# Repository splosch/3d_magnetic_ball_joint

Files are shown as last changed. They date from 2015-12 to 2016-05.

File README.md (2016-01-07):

# 3d_magnetic_ball_joint
Low-friction magnetic ball joints for delta 3d printer based on standard components

## information on the parts / examples
The assebled / example screens are indicate a scheme but might not contain the most recent part updates.
The 123DX and STL files reflect the latest updates.

## Design B: conic magnet with epoxy coating
Chromeball sliding directly on a epoxyd cylindric magnet with a conical hole where the ball snapps in

* Pro:
  * cheap standard components
  * ball is hold tight and is keept centered
  * N42 magnets provide enough stength to keep up with high printing speeds / accelerations
  * screw to maintain magnet holder pockets are reachable through magnet hole
* Contra:
  * potential wear from opertion on the epoxy coating
    * it's conical, not spherical so friction is not distributed equally
    * silikon lubrication or PTFE (Teflon) spray-paint-coating on top of the epoxy could help
  * in current design the magnet is press-fit in the pocket
    * A) tighten the screw leaves tiny traces from inserting/extrating screwdriver

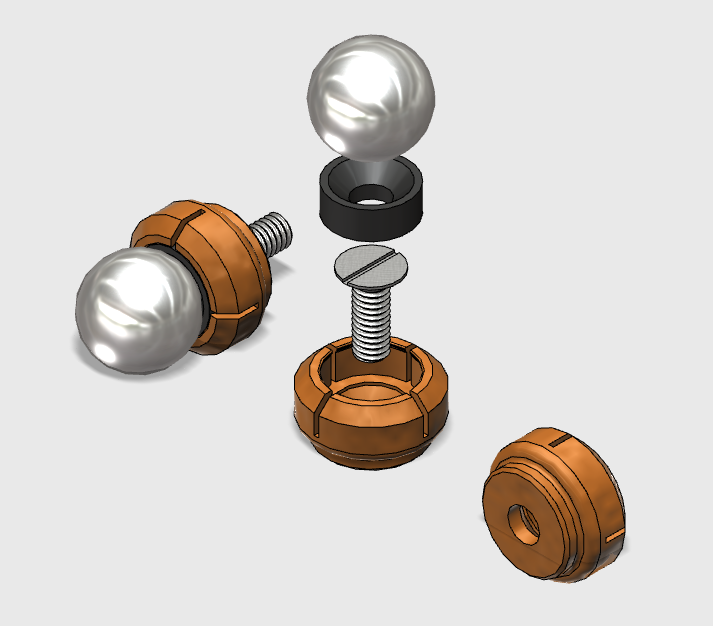
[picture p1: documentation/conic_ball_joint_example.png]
B) conic ball joint example


### Example: end effector
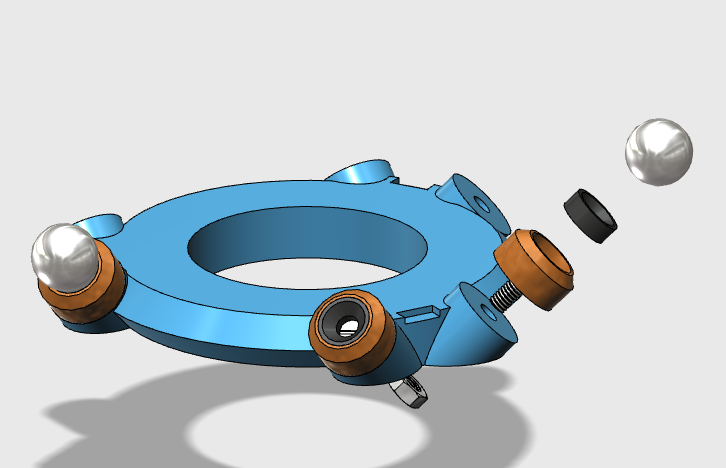
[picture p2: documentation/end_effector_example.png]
end effector example image


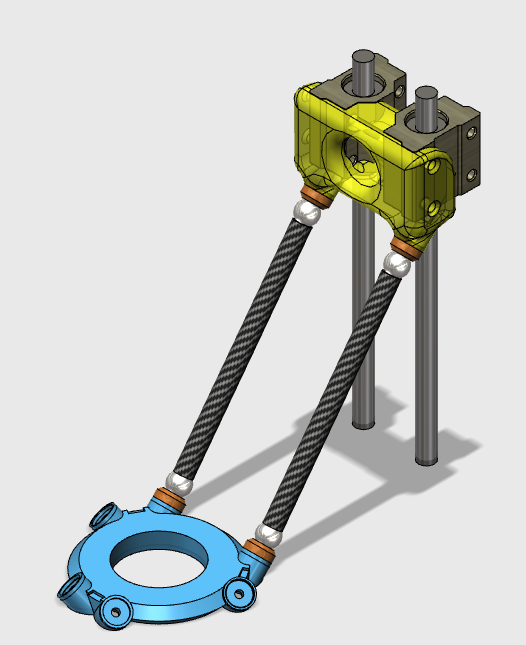
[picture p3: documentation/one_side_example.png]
end effector example image


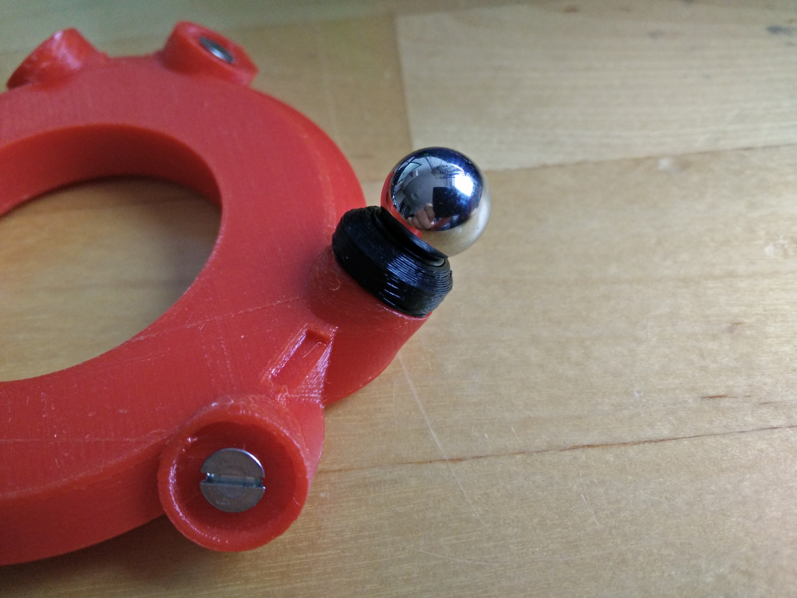
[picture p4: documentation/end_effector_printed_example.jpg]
end effector example printed


### BOM (Bill of materials)
Version B (Chromeball sliding on conic magnet coated in epoxy)
* 10mm Chrome-Steel-Ball
* 8 x 3mm conic Neodym-Magnet (N42 worked fine)
 * 45deg cone
 * 6.7mm top cone diameter
 * 3.5mm hole
* M3 Screw DIN 7991
* M3 Nut DIN 892 (tried a nylon one)

# Dropped Designs

## Design A: flat magnet with nylon washer (not working)
Chromeball sliding on a nylon washer, kept in place by a flat cylindric magnet
a 10mm ball sinks in the M6 nylon washers hole (6.2mm) with ~1.5mm thickness just far enough to not touch the magnet. Tight fit 6mm holes require ~1.2mm thickness.

* Pro:
  * cheap standard components
  * low friction
  * low wear on the washer --> little maintainance
* Contra:
  * the spacing that the washer and the spherical outline create is big
  * a 8x2mm N42 Magnet is not strong enough to hold the steelball tight
  * practical printing speeds / accelerations would not be possible
    * thicker magnets could help bridge the gap but add more weight

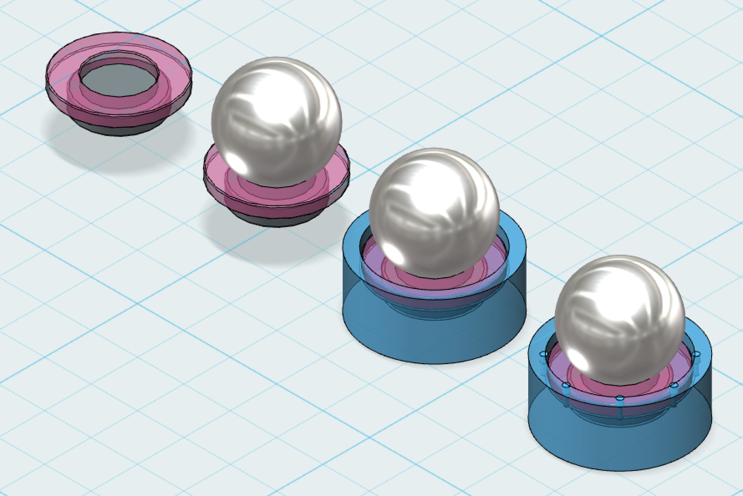
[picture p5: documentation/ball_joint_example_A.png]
A) ball joint example


### BOM (Bill of materials)
Design A (not working):
* 10mm Chrome-Steel-Ball
* 8 x 2mm Neodym-Magnet (for my purpose N50 worked fine)
* 11.9 x 1.5 mm M6 Nylon washer / disc
 * inner diameter 6.2mm

# Credits
* idea based on [Olooki3D](http://www.thingiverse.com/Olooki3D)'s design of a [Diamond magnetic effector for delta Kossel or Rostock **@ thingiverse**](http://www.thingiverse.com/thing:1157670)

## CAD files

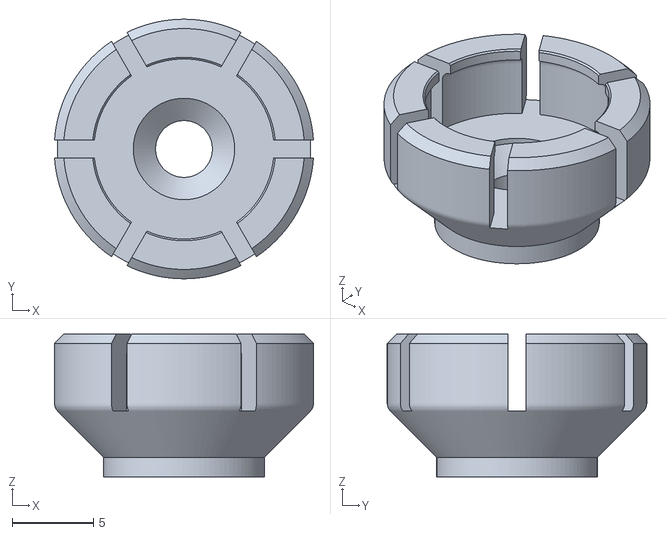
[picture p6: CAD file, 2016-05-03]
parts/conic_magnet_holder_12mm.stl
16.0 x 16.0 x 8.80

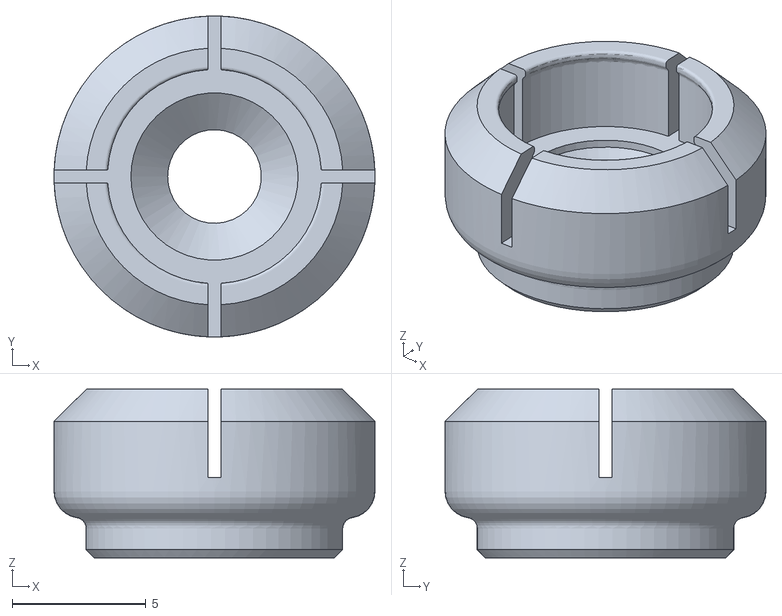
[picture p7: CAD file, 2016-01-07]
parts/conic_magnet_holder.stl
12.0 x 12.0 x 6.30

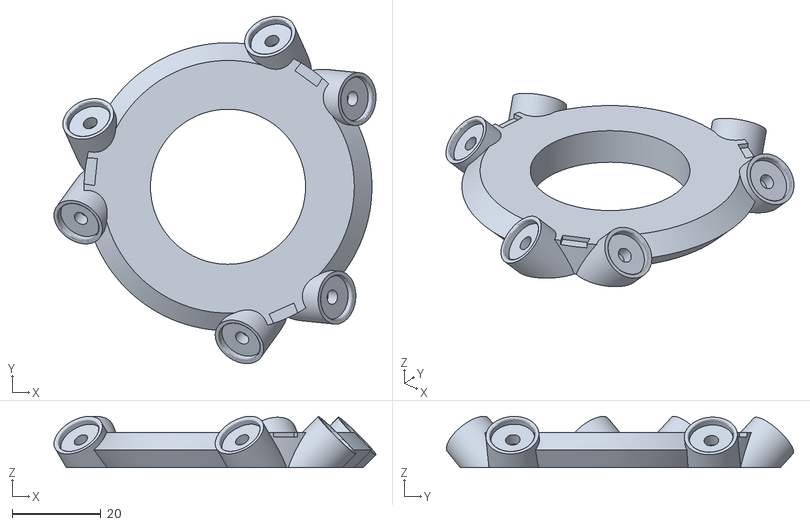
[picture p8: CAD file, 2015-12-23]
parts/end_effector.stl
72.7 x 78.4 x 11.6

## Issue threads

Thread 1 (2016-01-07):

Tighten screws will most likely scratch the magnet

splosch, 2016-01-07:

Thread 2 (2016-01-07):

Tight fit magnet holder adds lots of pressure to the magnet

splosch, 2016-01-07:
+ magnet could slip out due to temperature or usage / acceleration

Closed 2016-01-07.

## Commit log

2015-12-14 Initial idea of component based magnetic ball joints
    [magnet_holder.stl]
2015-12-17 Adapt design for greater precision in holding the nylon washer in place * add tension "lines" to the washer holder * add snap-in-place extrusion to tension lines * update part and example * add examp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
    [magnet_holder.stl]
2015-12-21 Resolve version conflict - drop tension bars for tension balls
    [magnet_holder.stl]
2015-12-22 Add conic magnet holder part, example img, end effector
    [conic_magnet_holder.stl, end_effector.stl]
2015-12-23 Add bits and bolts to the end effector example to outline assembly
2015-12-23 Added guidance to center the magnet holders on the end-effector-platform
    [conic_magnet_holder.stl, end_effector.stl]
2015-12-23 Differentiate between version A and B ball joint
2015-12-23 Added rod to join the end-effector
2015-12-31 Comment on reducing wear on the magnet via lubrication or PTFE coating
2015-12-31 Added photo of printed and partly assembled end-effector * move images into documentation folder
2016-01-04 Added bearing counterpart for the axis-pulley * based on existing linear-bearing bulley * model of pulley added * model of tight fit magnetic bearing holder created
2016-01-07 Fixes #2 Make the magnet snap in the pocket * add spacers and top notch to support snapping * updated stl
    [conic_magnet_holder.stl, magnet_holder.stl]
2016-01-07 Example of assembled pulley, rod, effector example
2016-01-14 Increase tolerances on pulley
2016-05-03 Add 12mm magnet holder
    [conic_magnet_holder_12mm.stl]
